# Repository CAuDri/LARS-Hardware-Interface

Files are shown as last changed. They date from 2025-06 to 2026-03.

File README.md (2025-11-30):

# LARS Hardware Interface

This repository contains the schematic, PCB design files and a basic firmware stack for the Hardware Interface of the [Lightweight Autonomous Racing System (LARS)](https://github.com/CAuDri/LARS). 

<p align="center">
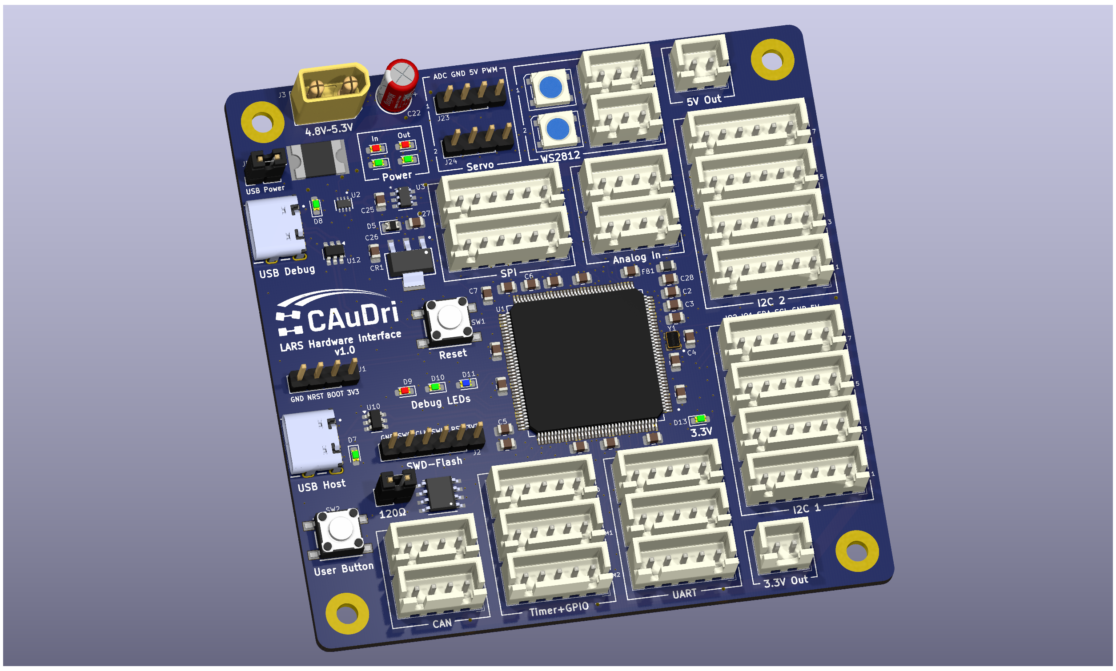
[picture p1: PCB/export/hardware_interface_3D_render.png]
  
</p>

The board is based on a STM32F4 microcontroller and is designed to interface with various sensors and actuators on the vehicle. The communication with the host PC is done via USB, using [micro-ROS](https://micro.ros.org/) and the underlying [micro-XRCE DDS](https://micro-xrce-dds.docs.eprosima.com/en/latest/).

## License

This project is licensed under the [GNU General Public License v3.0](https://www.gnu.org/licenses/gpl-3.0.en.html). You can freely use, modify, and distribute this code as long as you comply with the terms of the license.

The hardware design files are released under the [CERN Open Hardware Licence v2](https://ohwr.org/cernohl/).

# Hardware

##  Features

### General
- STM32F429 microcontroller (Cortex-M4, 180MHz, 2MB Flash, 256KB RAM)
- Board dimensions: 86 x 86 mm
- SWD interface for programming and debugging
- Boot-/Reset header for flashing via USB
- User- and Reset buttons
- RGB Debug LEDs

### Power
- 5V power supply via XT30 connector or USB (XT30 will be prioritized)
- Power input range: **4.8V - 5.3V**
- "Reverse polarity protection"
- On-board 3.3V voltage regulator
- Switchable 5V output for external devices
- Additional 3.3V and 5V output

### Interfaces
- 2x USB-C (2.0 Fullspeed) for host PC and debugging/flashing
- CAN-Bus (with optional termination)
- 8x I2C
- 3x UART
- 2x SPI
- 2x Servo (with analog feedback)
- 2x WS2812 LED strip 
- Buffered and filtered analog inputs
- Additional Timer channels and GPIOs
- 3.3V and 5V output for external devices

### Protection
- 4A/8A polyfuse on the main power input
- "Rudimentary" reverse polarity protection
- Back-power protection for both power inputs (USB and XT30)
- TVS diodes against voltage spikes on all power rails
- Current limited 5V output (max 2.4 A)
- All data lines are 5V tolerant
- Additional short-circuit, overcurrent and -voltage protection up to ~20V on all interfaces

## PCB-Files

The board was designed in KiCad 9.0. The project file can be found in the `/PCB/KiCad` directory.

Link to the [Schematic](https://github.com/CAuDri/LARS-Hardware-Interface/blob/main/PCB/schematic.pdf).

All PCB design files, a bill of materials and Gerber Files for manufacturing at [JLCPCB](https://jlcpcb.com/) can be found in the `/PCB/manufacturing` directory. They have been exported using the [Fabrication Toolkit](https://github.com/bennymeg/Fabrication-Toolkit) KiCad plugin.

A 3D STEP model of the board can be found in the `/PCB/export` directory.

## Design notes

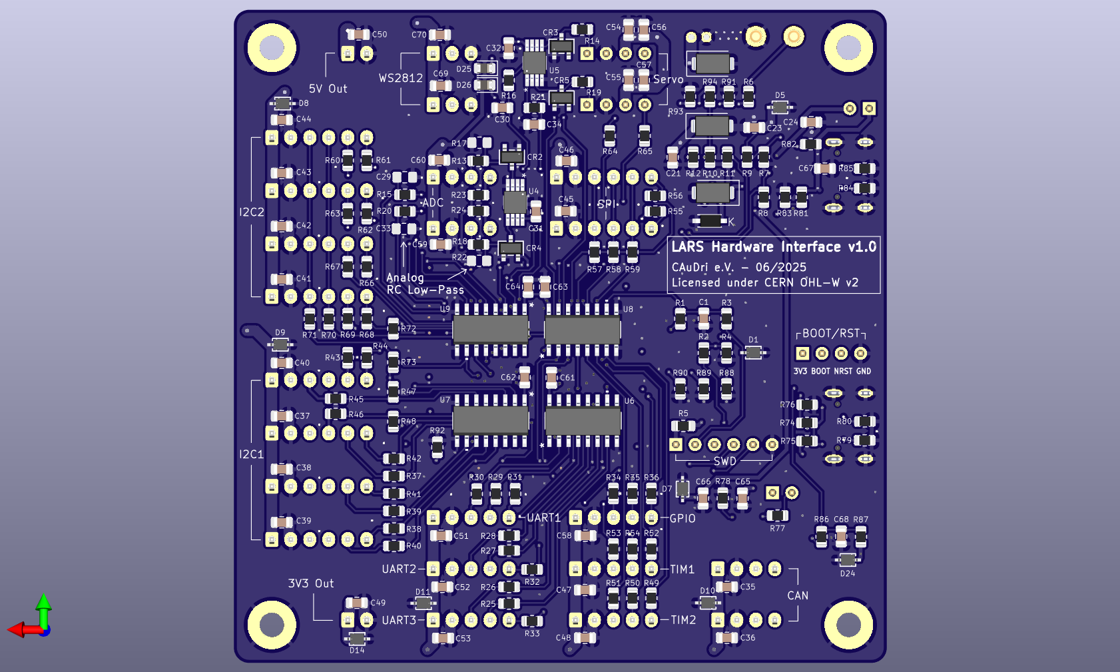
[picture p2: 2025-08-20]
PCB/export/hardware_interface_3D_back.png

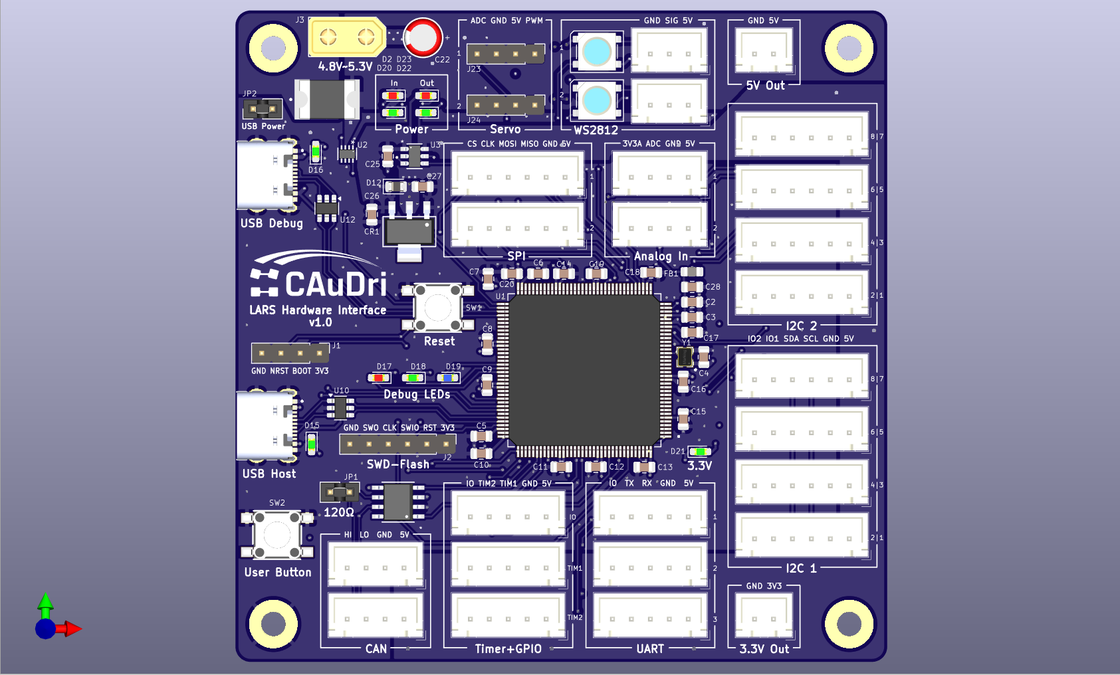
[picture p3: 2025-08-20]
PCB/export/hardware_interface_3D_front.png

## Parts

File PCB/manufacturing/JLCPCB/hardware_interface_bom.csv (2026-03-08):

Designator | Footprint | Quantity | Value | LCSC Part #
C1, C10, C11, C12, C13, C14, C15, C16, C17, C18, C19, C20, C3, C30, C31, C32, C34, C35, C36, C37, C38, C39, C4, C40, C41, C42, C43, C44, C45, C46, C47, C48, C49, C50, C51, C52, C53, C54, C57, C58, C59, C60, C61, C62, C63, C64, C65, C66, C67, C70, C71, C8, C9 | 0805 | 53 | 100n
C2, C24, C26, C5, C6, C68, C69 | 0805 | 7 | 2u2
C21, C23, C25, C27, C55, C56, C7 | 0805 | 7 | 10u
C22 | 860020372006 | 1 | 100u
C28 | 0805 | 1 | 10n
CR1 | LD1117AS33TR | 1 | LD1117AS33TR
CR2, CR3, CR4, CR5 | BAT54SFILM | 4 | BAT54SFILM
D1, D10, D11, D14, D24, D5, D7, D8, D9 | STS321050U182 | 9 | TVS
D12, D25, D26 | 0805 | 3 | 0.7V
D13 | BZT52C3V3 | 1 | 3V3
D15, D16, D18, D20, D21, D22 | 0603 | 6 | Green
D17, D2, D23 | 0603 | 3 | Red
D19 | 0603 | 1 | Blue
D27, D28 | LED_WS2812B_PLCC4_5.0x5.0mm_P3.2mm | 2 | WS2812B
D3, D4, D6 | Z1SMA5.6 | 3 | 5V6
F1 | 2920L400_15MR | 1 | 2920L400
FB1 | 0805 | 1 | FBMH2012HM221-T8
G1 | CAuDri Logo | 1 | CAuDri-Logo
G2 | OSHWA Logo | 1 | LOGO
J1 | PinHeader_1x04_P2.54mm_Vertical | 1 | Reset Header
J10, J11, J8, J9 | JST_XH_B6B-XH-A_1x06_P2.50mm_Vertical | 4 | I2C1
J12 | JST_XH_B5B-XH-A_1x05_P2.50mm_Vertical | 1 | TIM1
J13 | JST_XH_B5B-XH-A_1x05_P2.50mm_Vertical | 1 | TIM2
J14, J15, J16, J17 | JST_XH_B6B-XH-A_1x06_P2.50mm_Vertical | 4 | I2C2
J18 | JST_XH_B2B-XH-A_1x02_P2.50mm_Vertical | 1 | 3.3V Out
J19 | JST_XH_B2B-XH-A_1x02_P2.50mm_Vertical | 1 | 5V Out
J2 | PinHeader_1x06_P2.54mm_Vertical | 1 | SWD Flash
J20 | JST_XH_B5B-XH-A_1x05_P2.50mm_Vertical | 1 | UART1
J21 | JST_XH_B5B-XH-A_1x05_P2.50mm_Vertical | 1 | UART2
J22 | JST_XH_B5B-XH-A_1x05_P2.50mm_Vertical | 1 | RC
J23 | JST_XH_B5B-XH-A_1x05_P2.50mm_Vertical | 1 | GPIO
J24 | PinHeader_1x04_P2.54mm_Vertical | 1 | Servo 1
J25 | PinHeader_1x04_P2.54mm_Vertical | 1 | Servo 2
J26 | JST_XH_B4B-XH-A_1x04_P2.50mm_Vertical | 1 | Analog 1
J27 | JST_XH_B4B-XH-A_1x04_P2.50mm_Vertical | 1 | Analog 2
J28 | GCT_USB4105-GF-A | 1 | USB1
J29 | GCT_USB4105-GF-A | 1 | USB2
J3 | XT30UPB-M | 1 | XT30
J30 | JST_XH_B3B-XH-A_1x03_P2.50mm_Vertical | 1 | LED1
J31 | JST_XH_B3B-XH-A_1x03_P2.50mm_Vertical | 1 | LED2
J4, J5 | JST_XH_B4B-XH-A_1x04_P2.50mm_Vertical | 2 | CAN1
J6, J7 | JST_XH_B6B-XH-A_1x06_P2.50mm_Vertical | 2 | SPI1
JP1 | PinHeader_1x02_P2.54mm_Jumper | 1 | CAN1
JP2 | PinHeader_1x02_P2.54mm_Jumper | 1 | USB Power
R1, R4, R7, R86 | 0805 | 4 | 10k
R10, R11, R79, R8, R80, R84, R85 | 0805 | 7 | 5k1
R12, R23, R24, R44, R45, R68, R69, R77 | 0805 | 8 | 120
R13, R14, R16, R18, R19, R2, R21, R6, R74, R78, R81, R87, R88, R89, R9, R90, R91, R92, R93, R94 | 0805 | 20 | 1k
R15, R20, R25, R26, R27, R28, R29, R3, R30, R31, R32, R33, R34, R35, R36, R37, R38, R39, R40, R41, R42, R43, R48, R49, R50, R51, R52, R53, R54, R55, R56, R57, R58, R59, R60, R61, R62, R63, R64, R65, R66, R67, R72, R73, R75, R82 | 0805 | 46 | 220
R46, R47, R70, R71, R76, R83 | 0805 | 6 | 2k2
R5 | 0805 | 1 | 0R
SW1 | 430182043816 | 1 | Reset
SW2 | 430182043816 | 1 | User Button
U1 | STM32F429ZIT6TR | 1 | STM32F429ZIT6TR
U10 | SN74LVC2G86 | 1 | SN74LVC2G86DCUR
U11, U13 | SOT-23-6 | 2 | USBLC6-2SC6
U12 | TCAN1057AVDRQ1 | 1 | TCAN1057AVDRQ1
U2 | PTPS2117DRLR | 1 | TPS2117DRLR
U3 | MIC2039AYM6-TR | 1 | MIC2039AYM6-TR
U4, U5 | OPA2834IDGKR | 2 | OPA2834IDGKR
U6, U7, U8, U9 | SN74S1051DR | 4 | SN74S1051DR
Y1 | WE-SPXO_IQXO-791 | 1 | IQXO-791 8.00MHz

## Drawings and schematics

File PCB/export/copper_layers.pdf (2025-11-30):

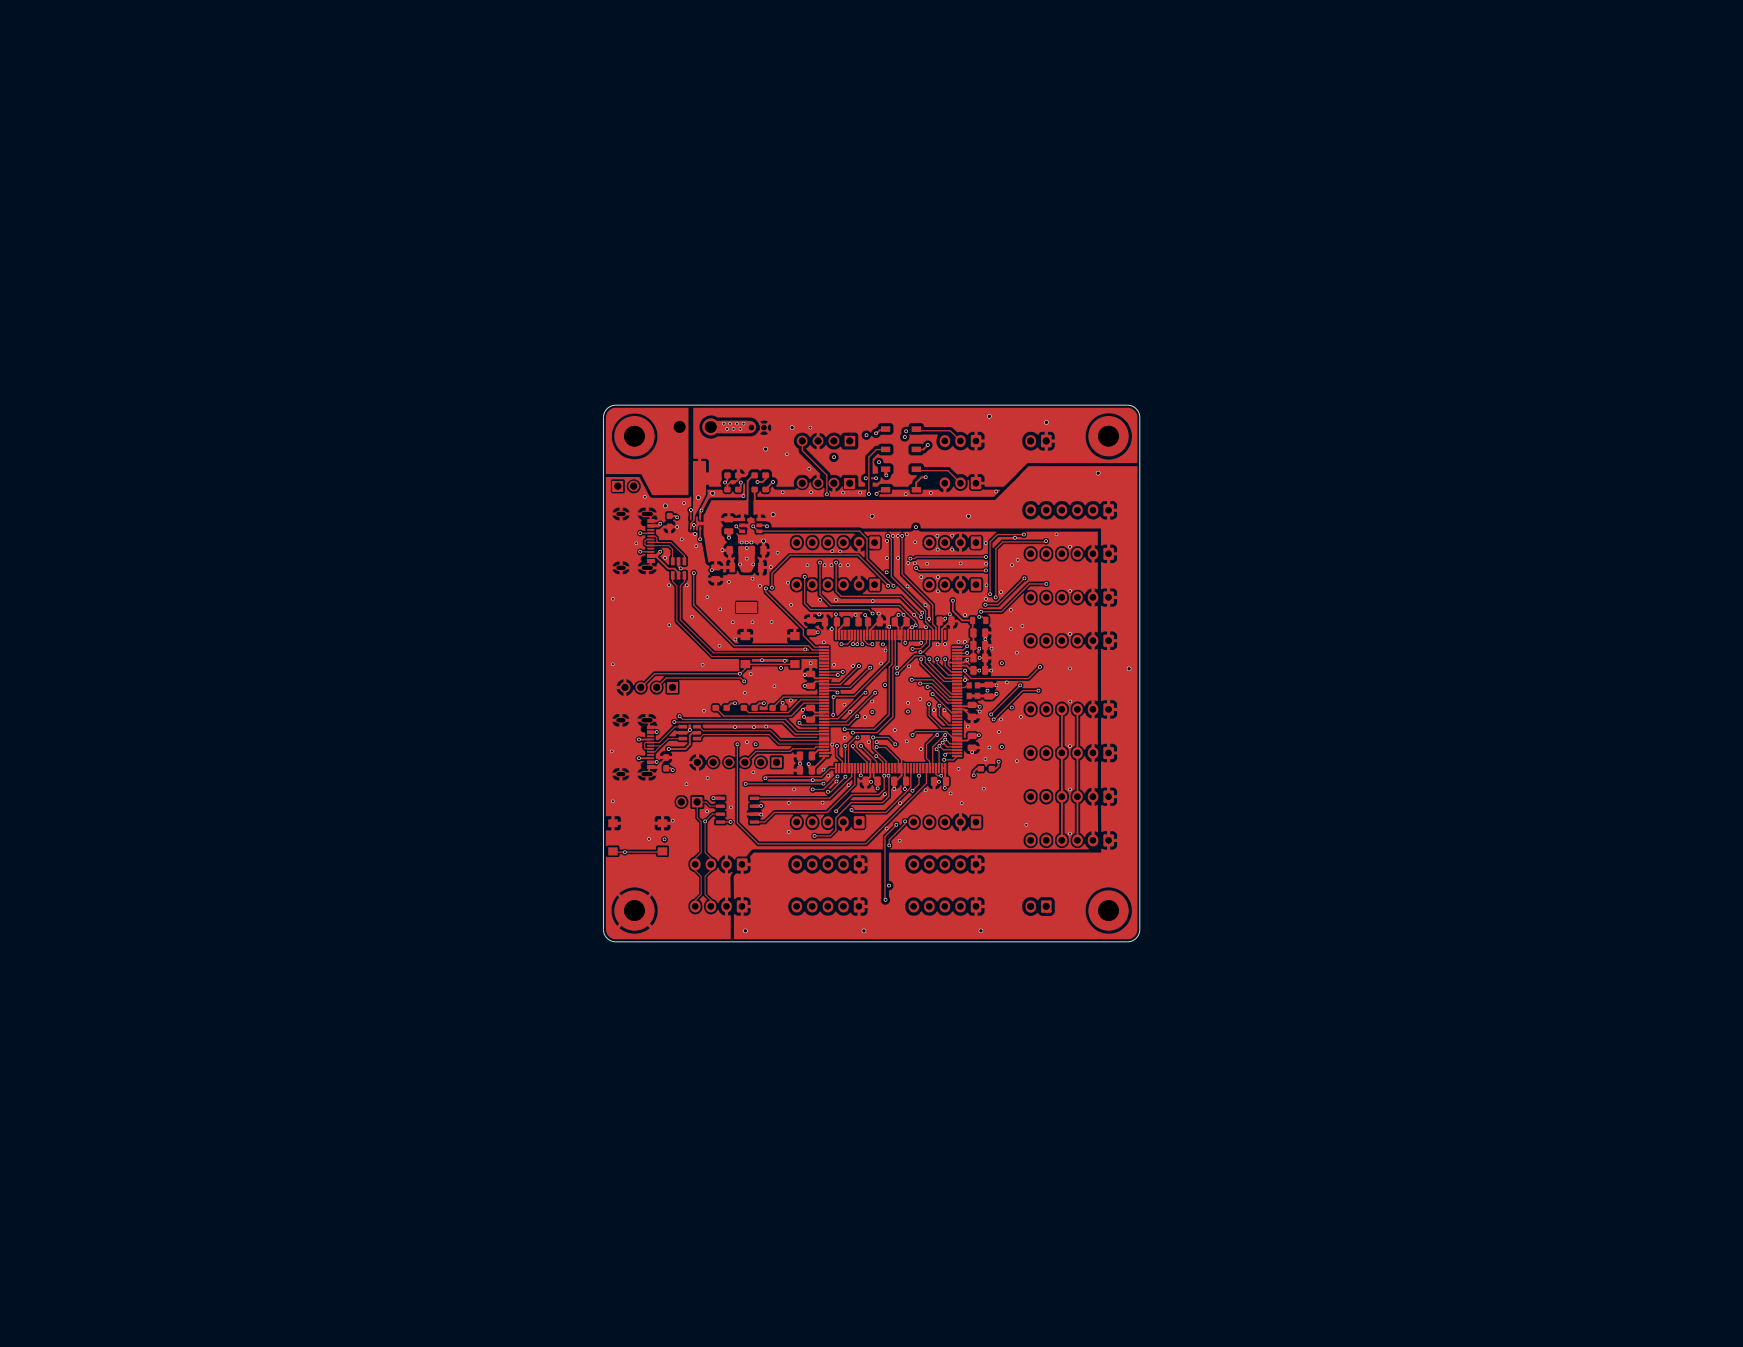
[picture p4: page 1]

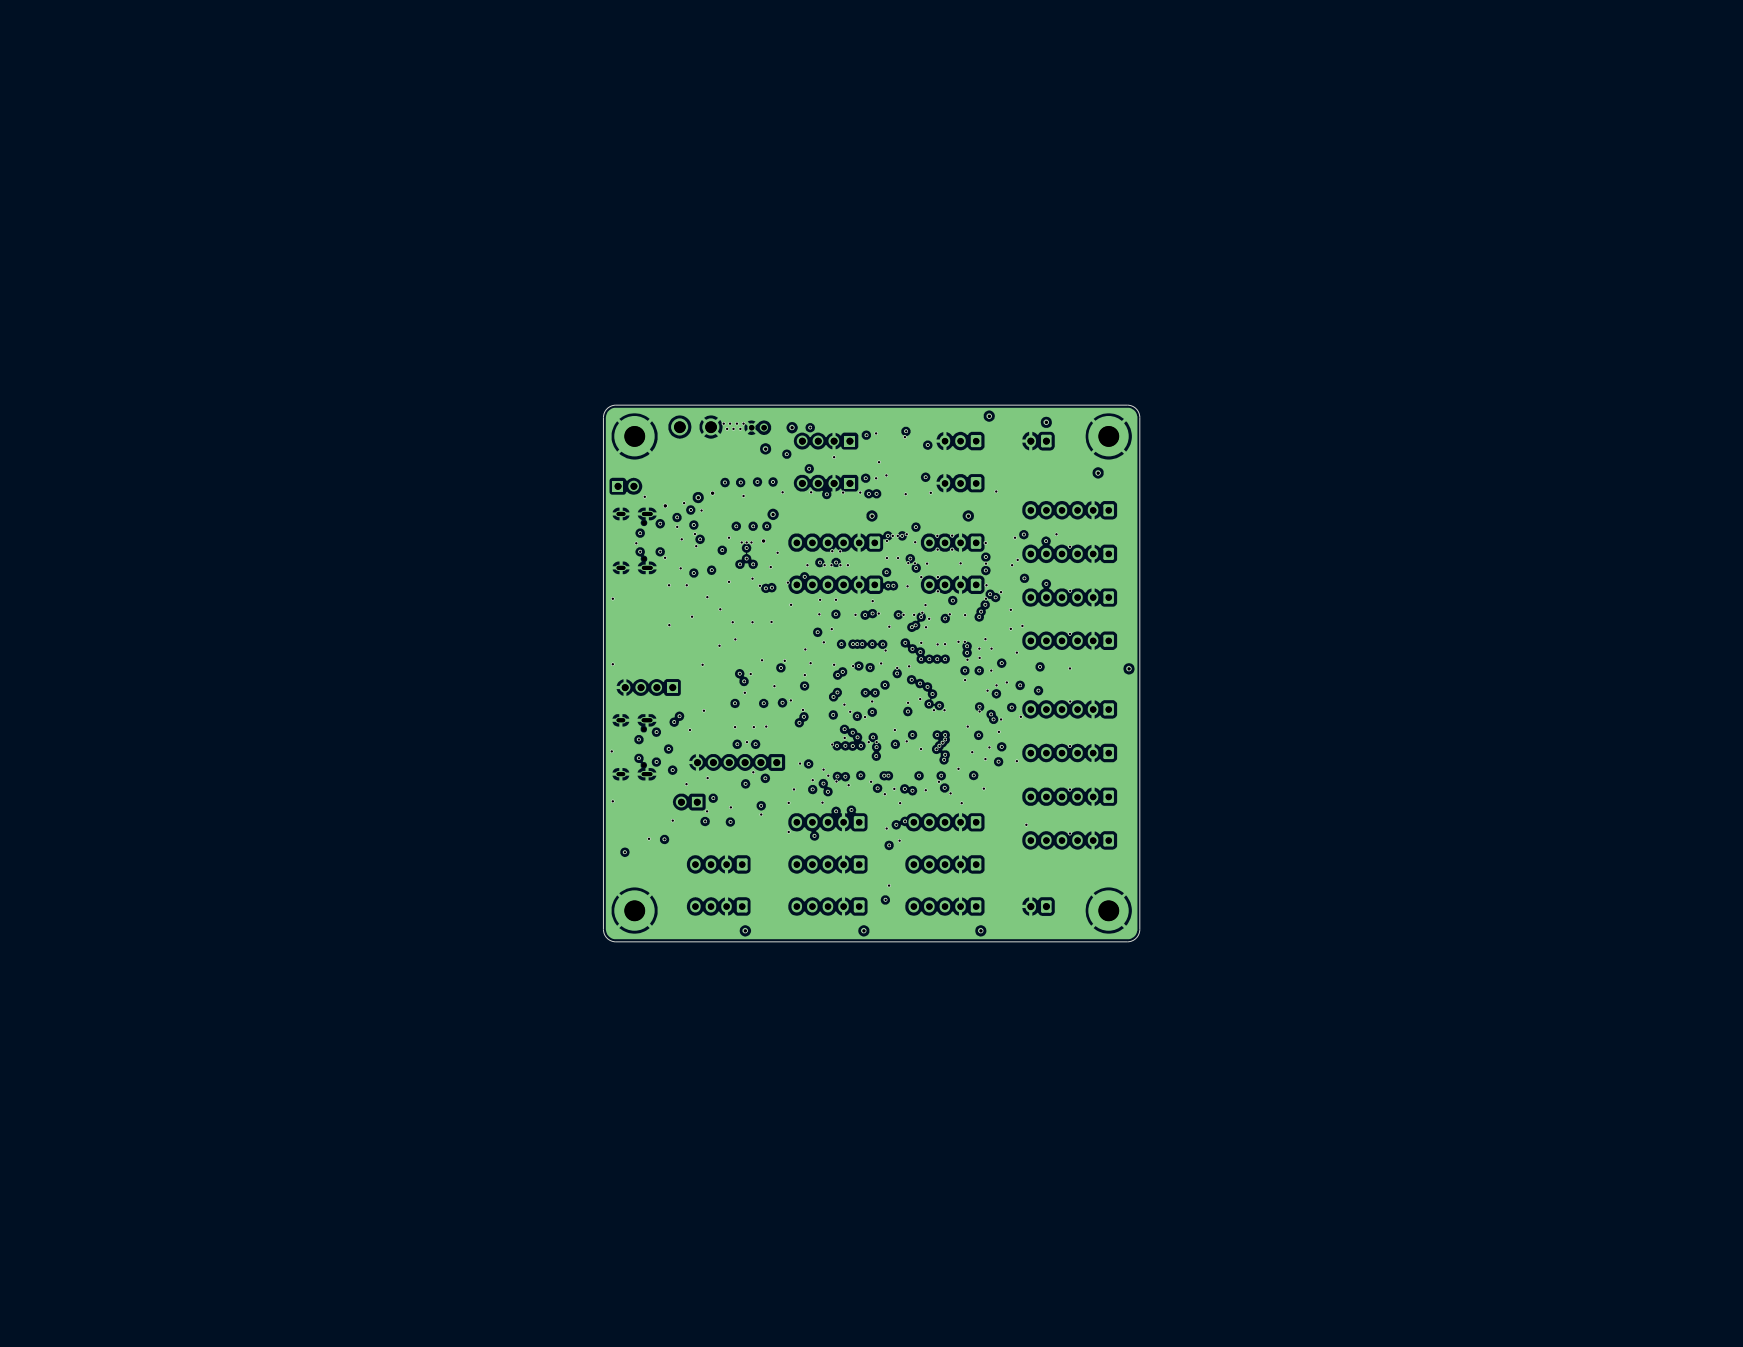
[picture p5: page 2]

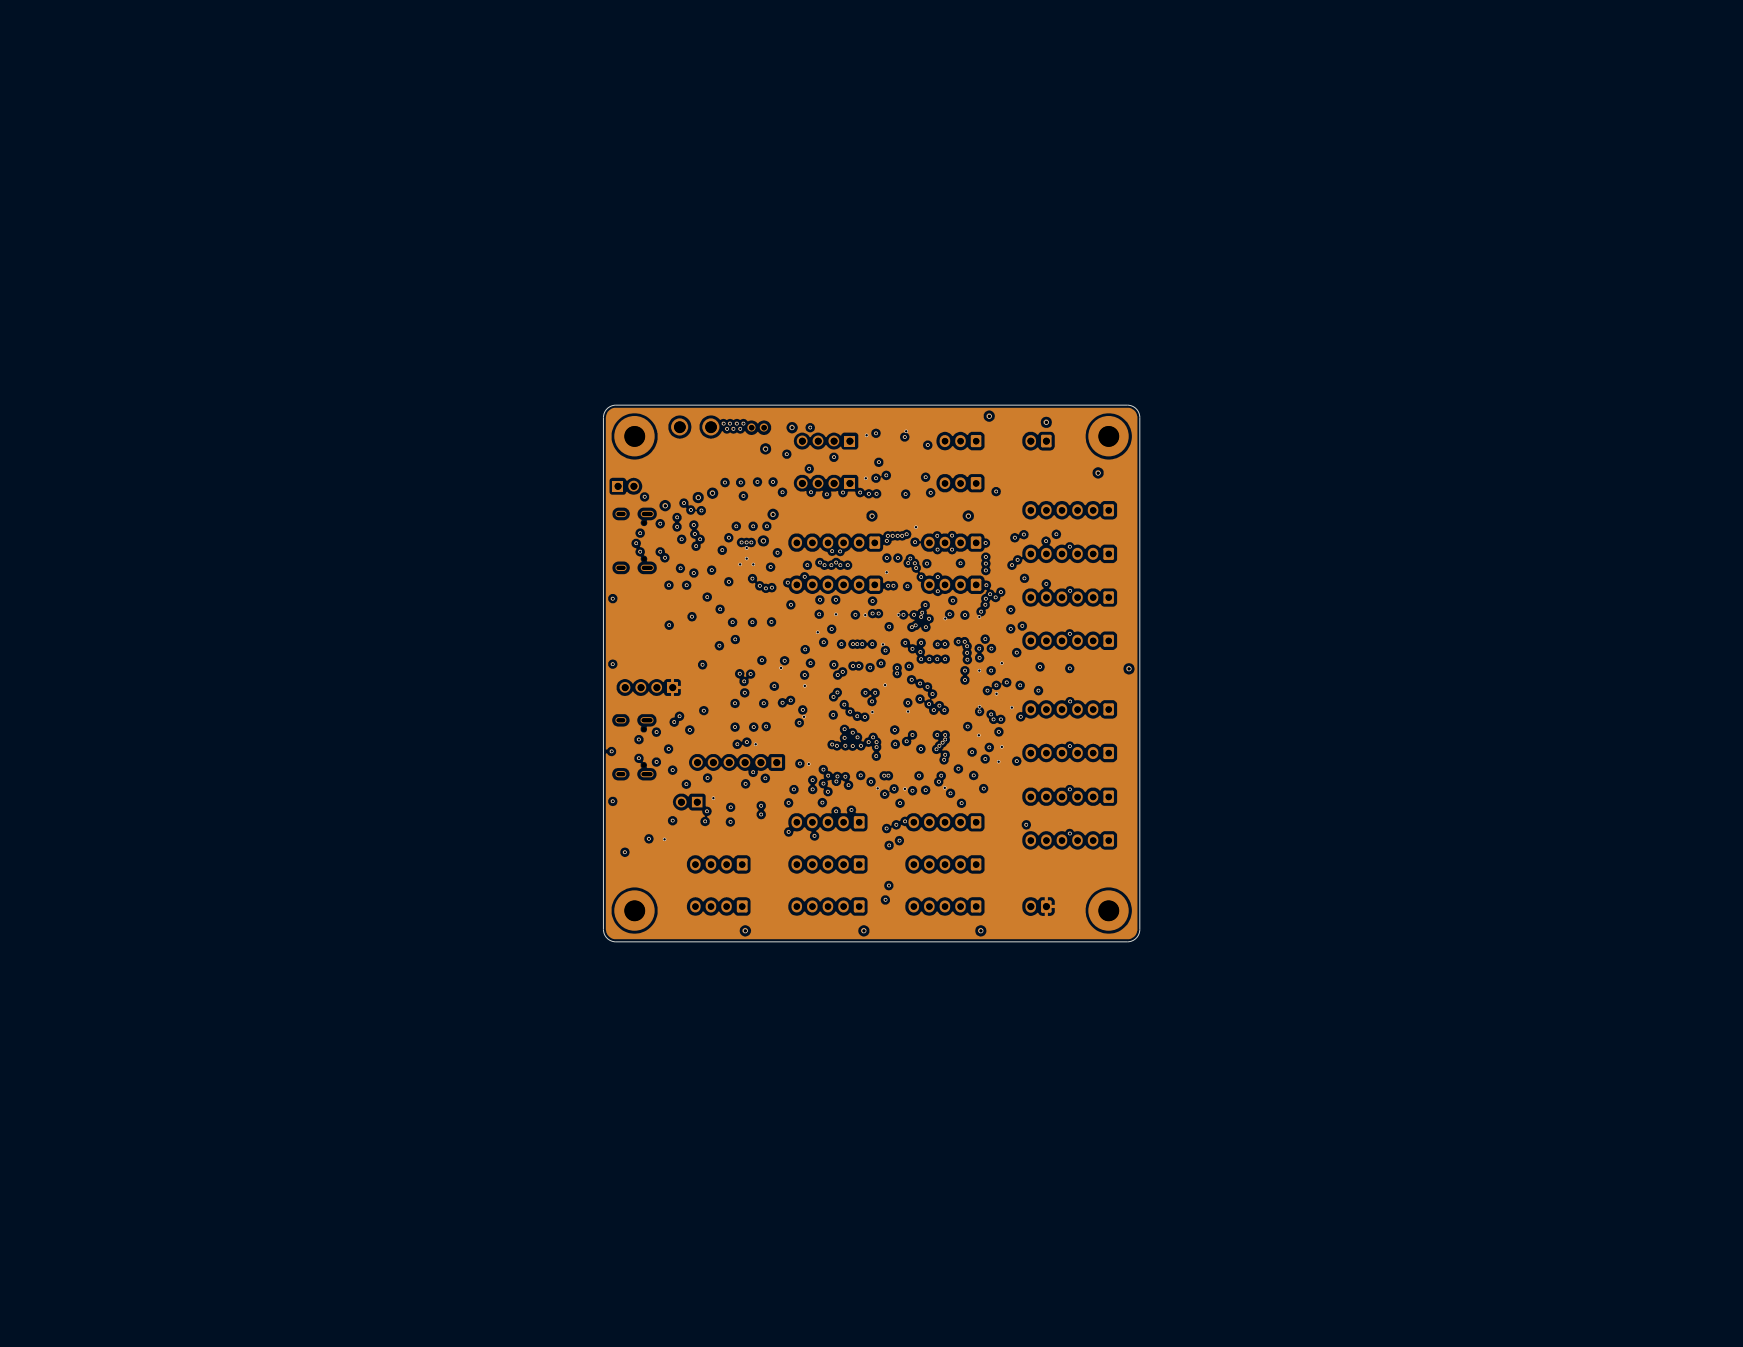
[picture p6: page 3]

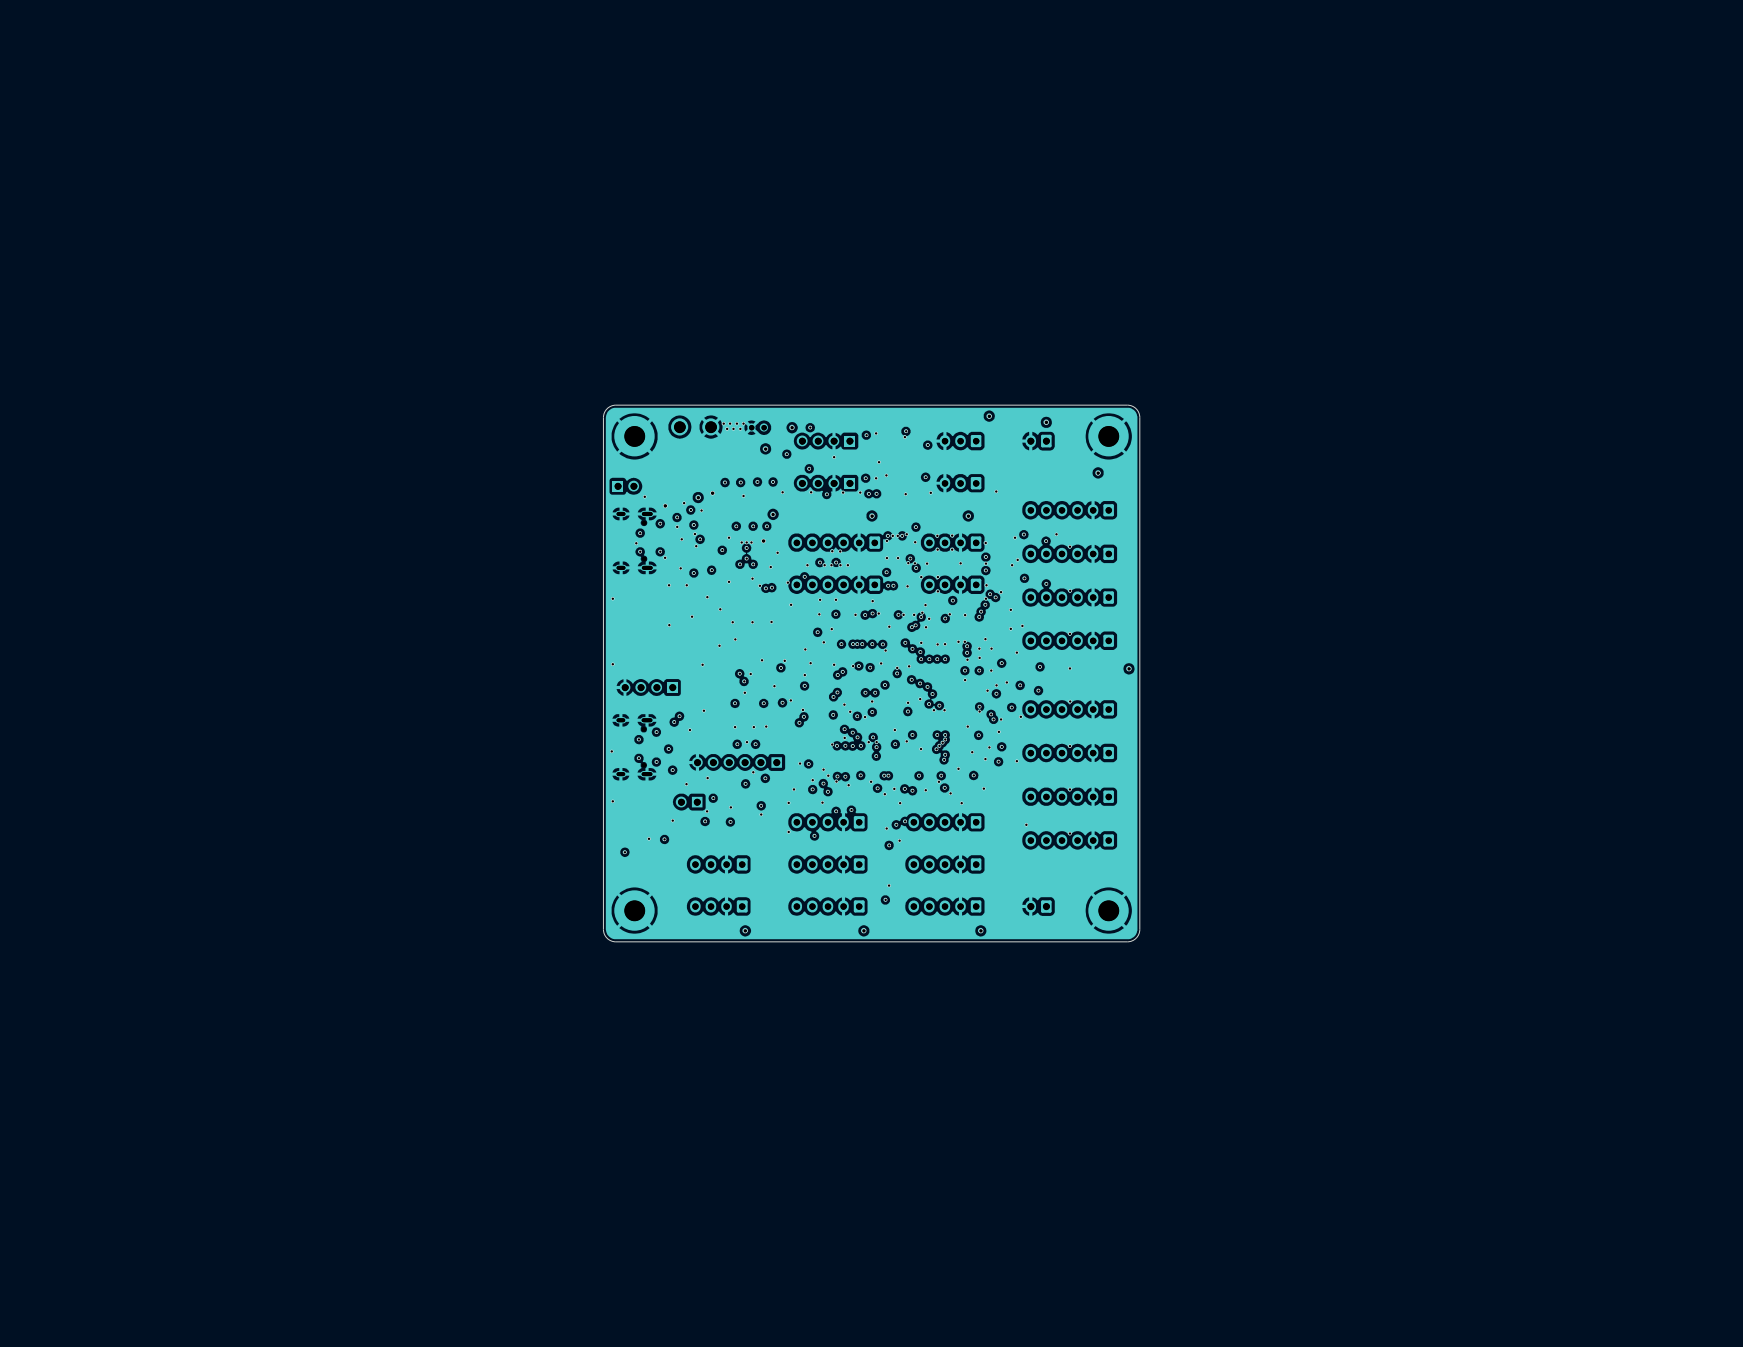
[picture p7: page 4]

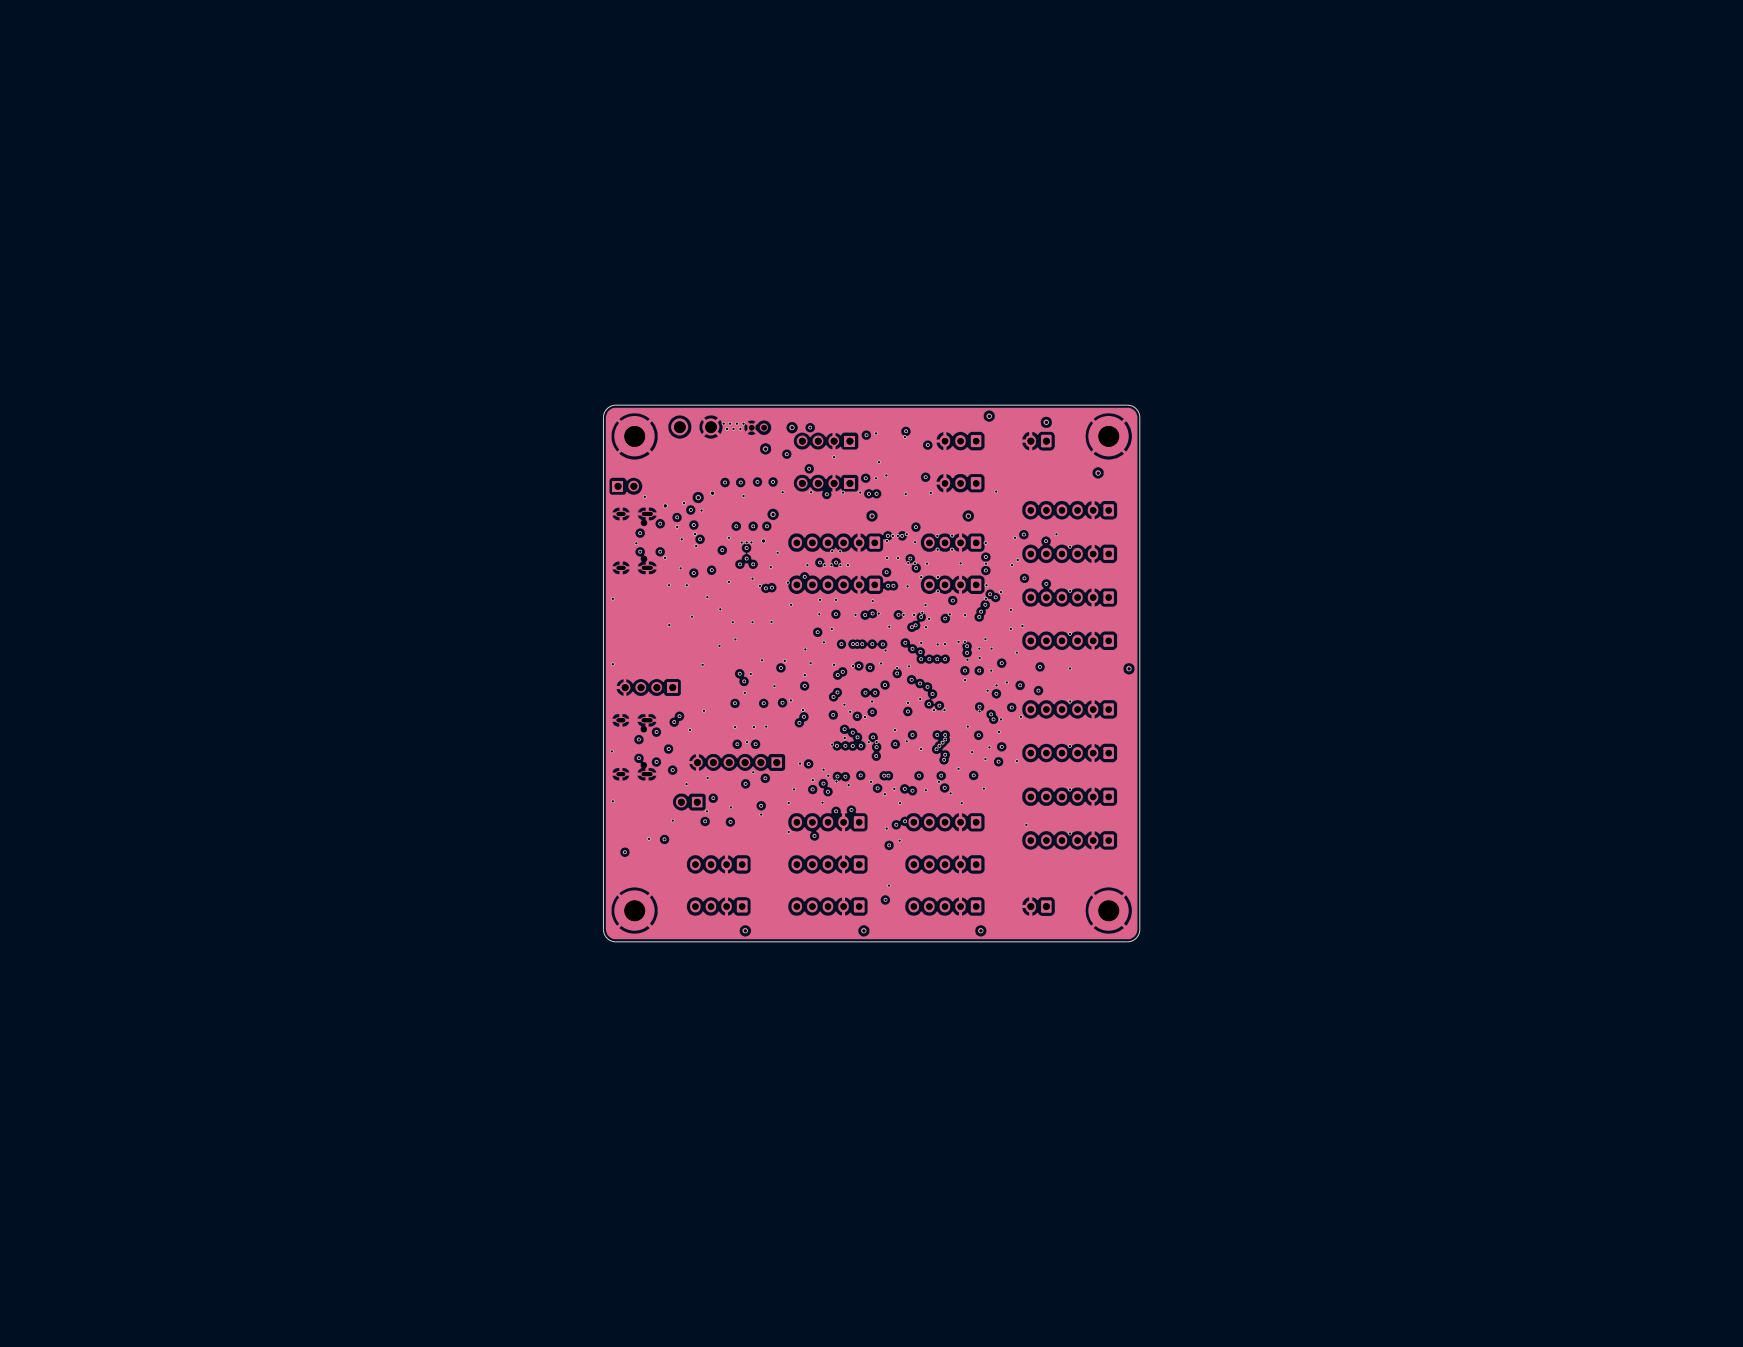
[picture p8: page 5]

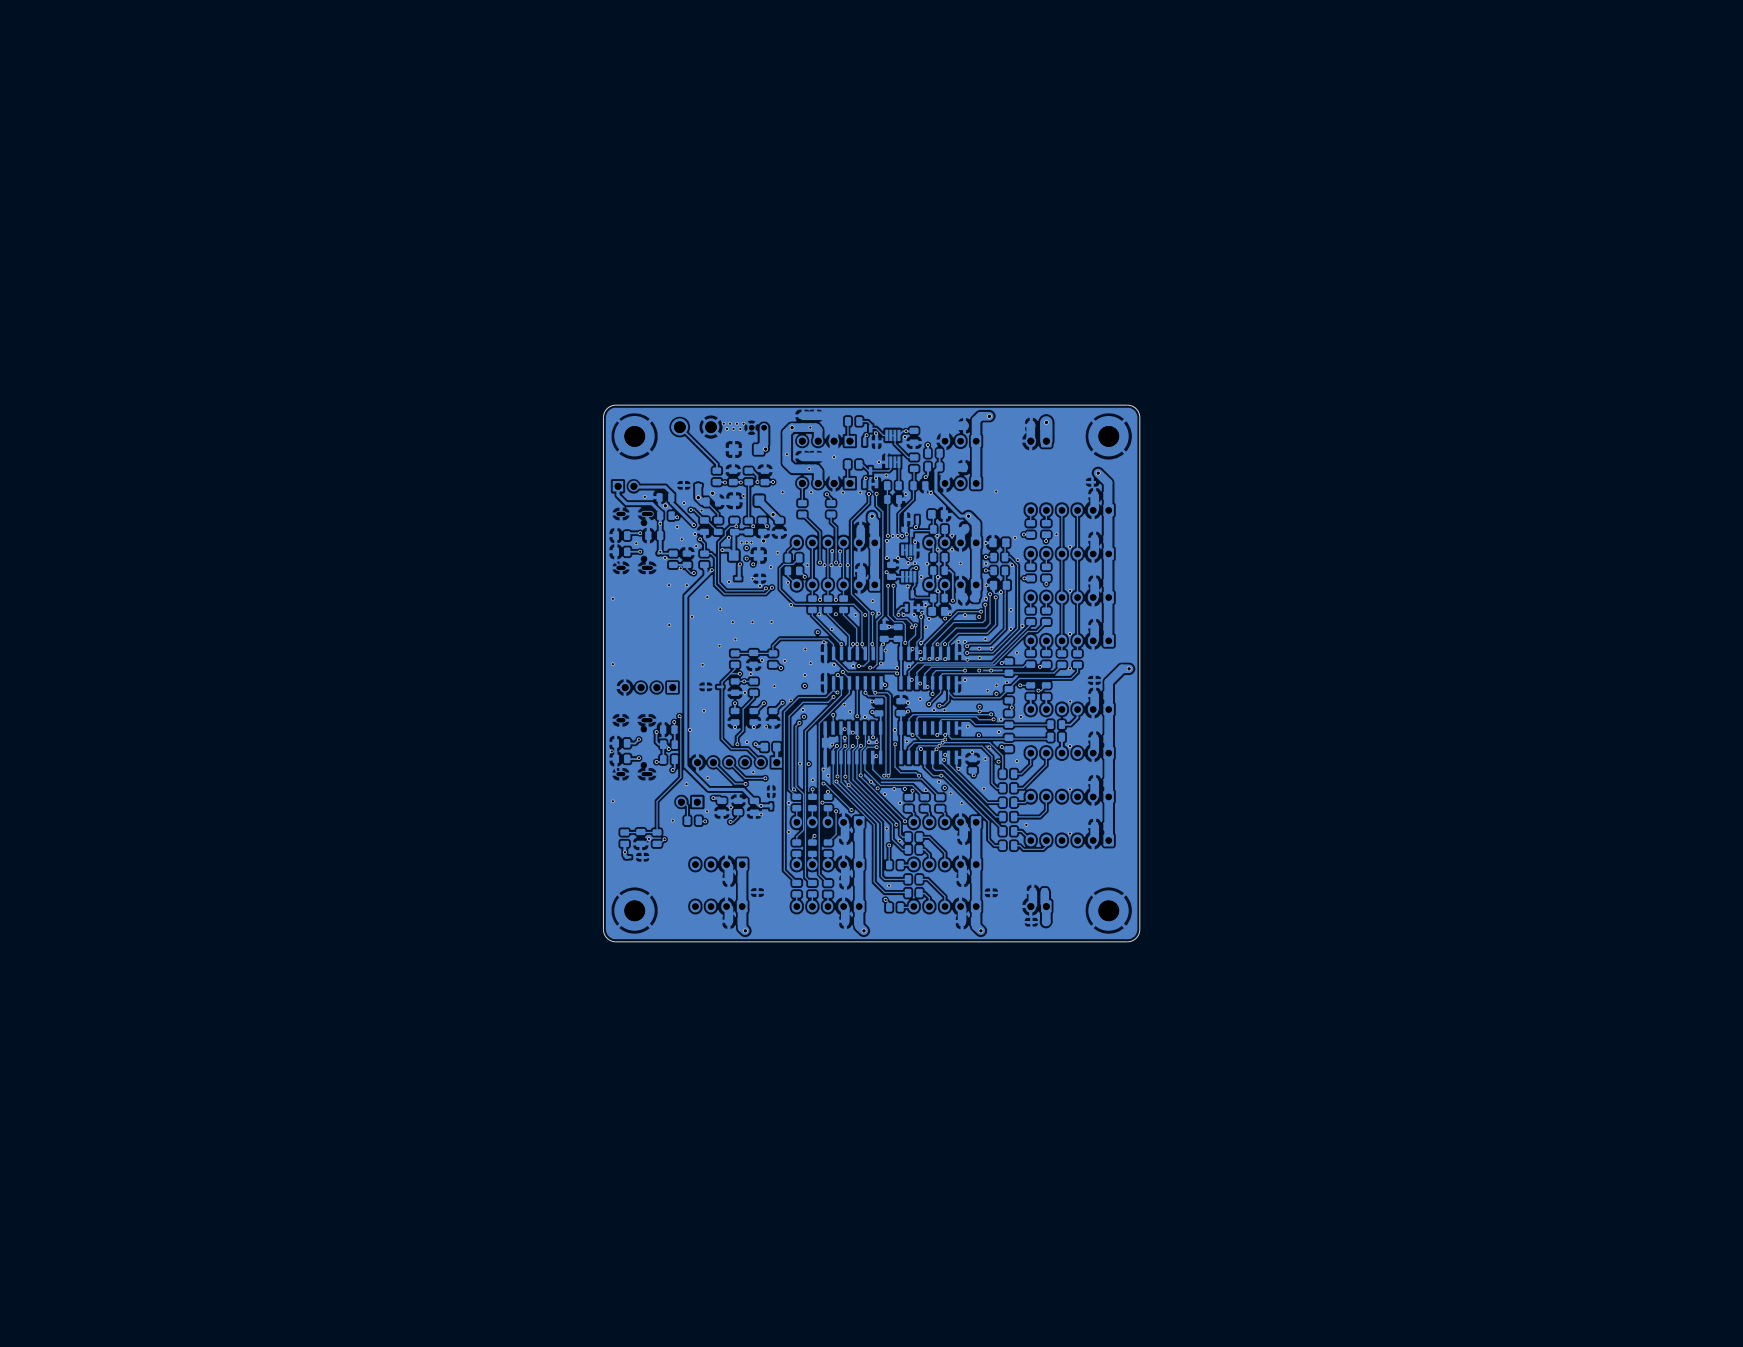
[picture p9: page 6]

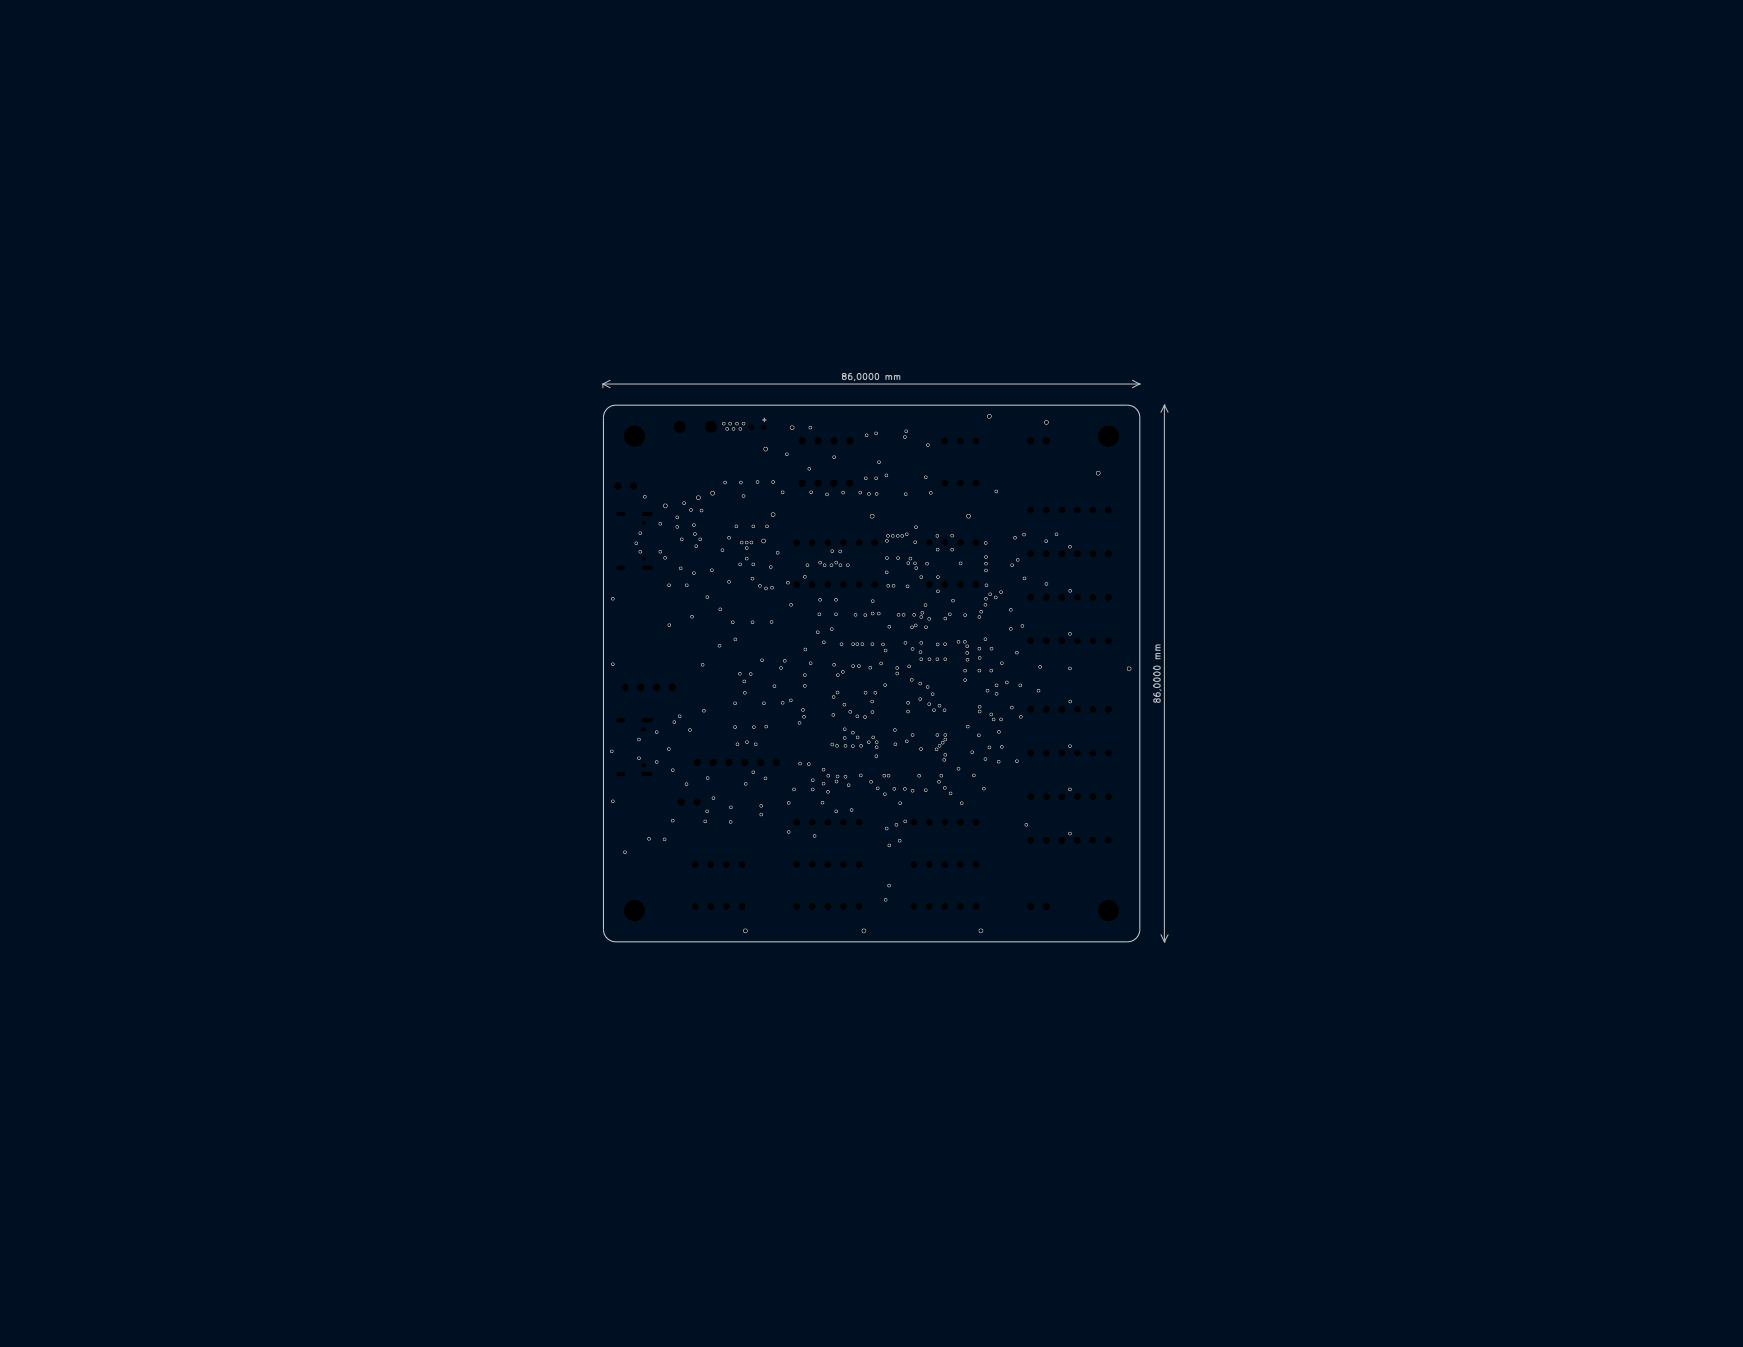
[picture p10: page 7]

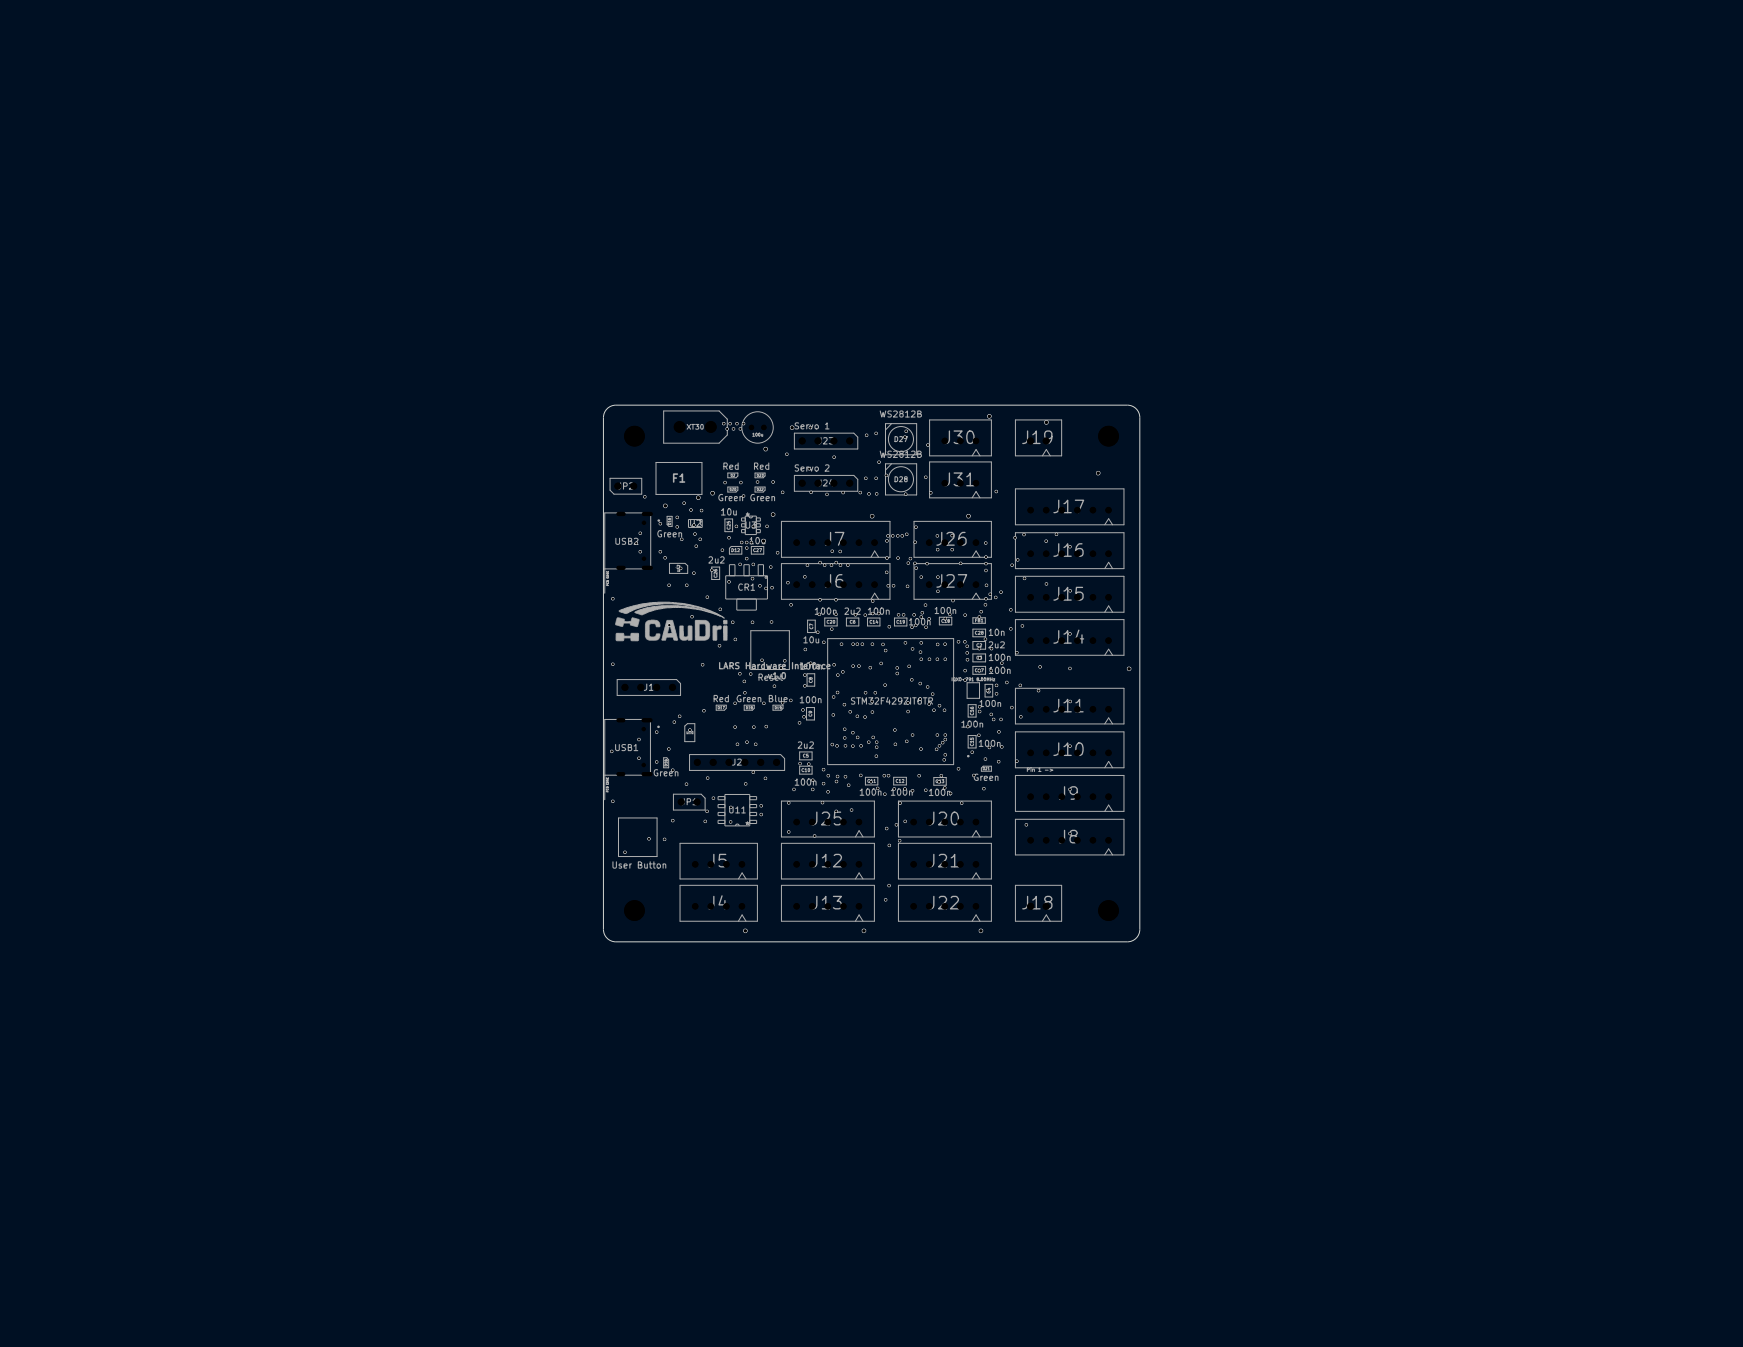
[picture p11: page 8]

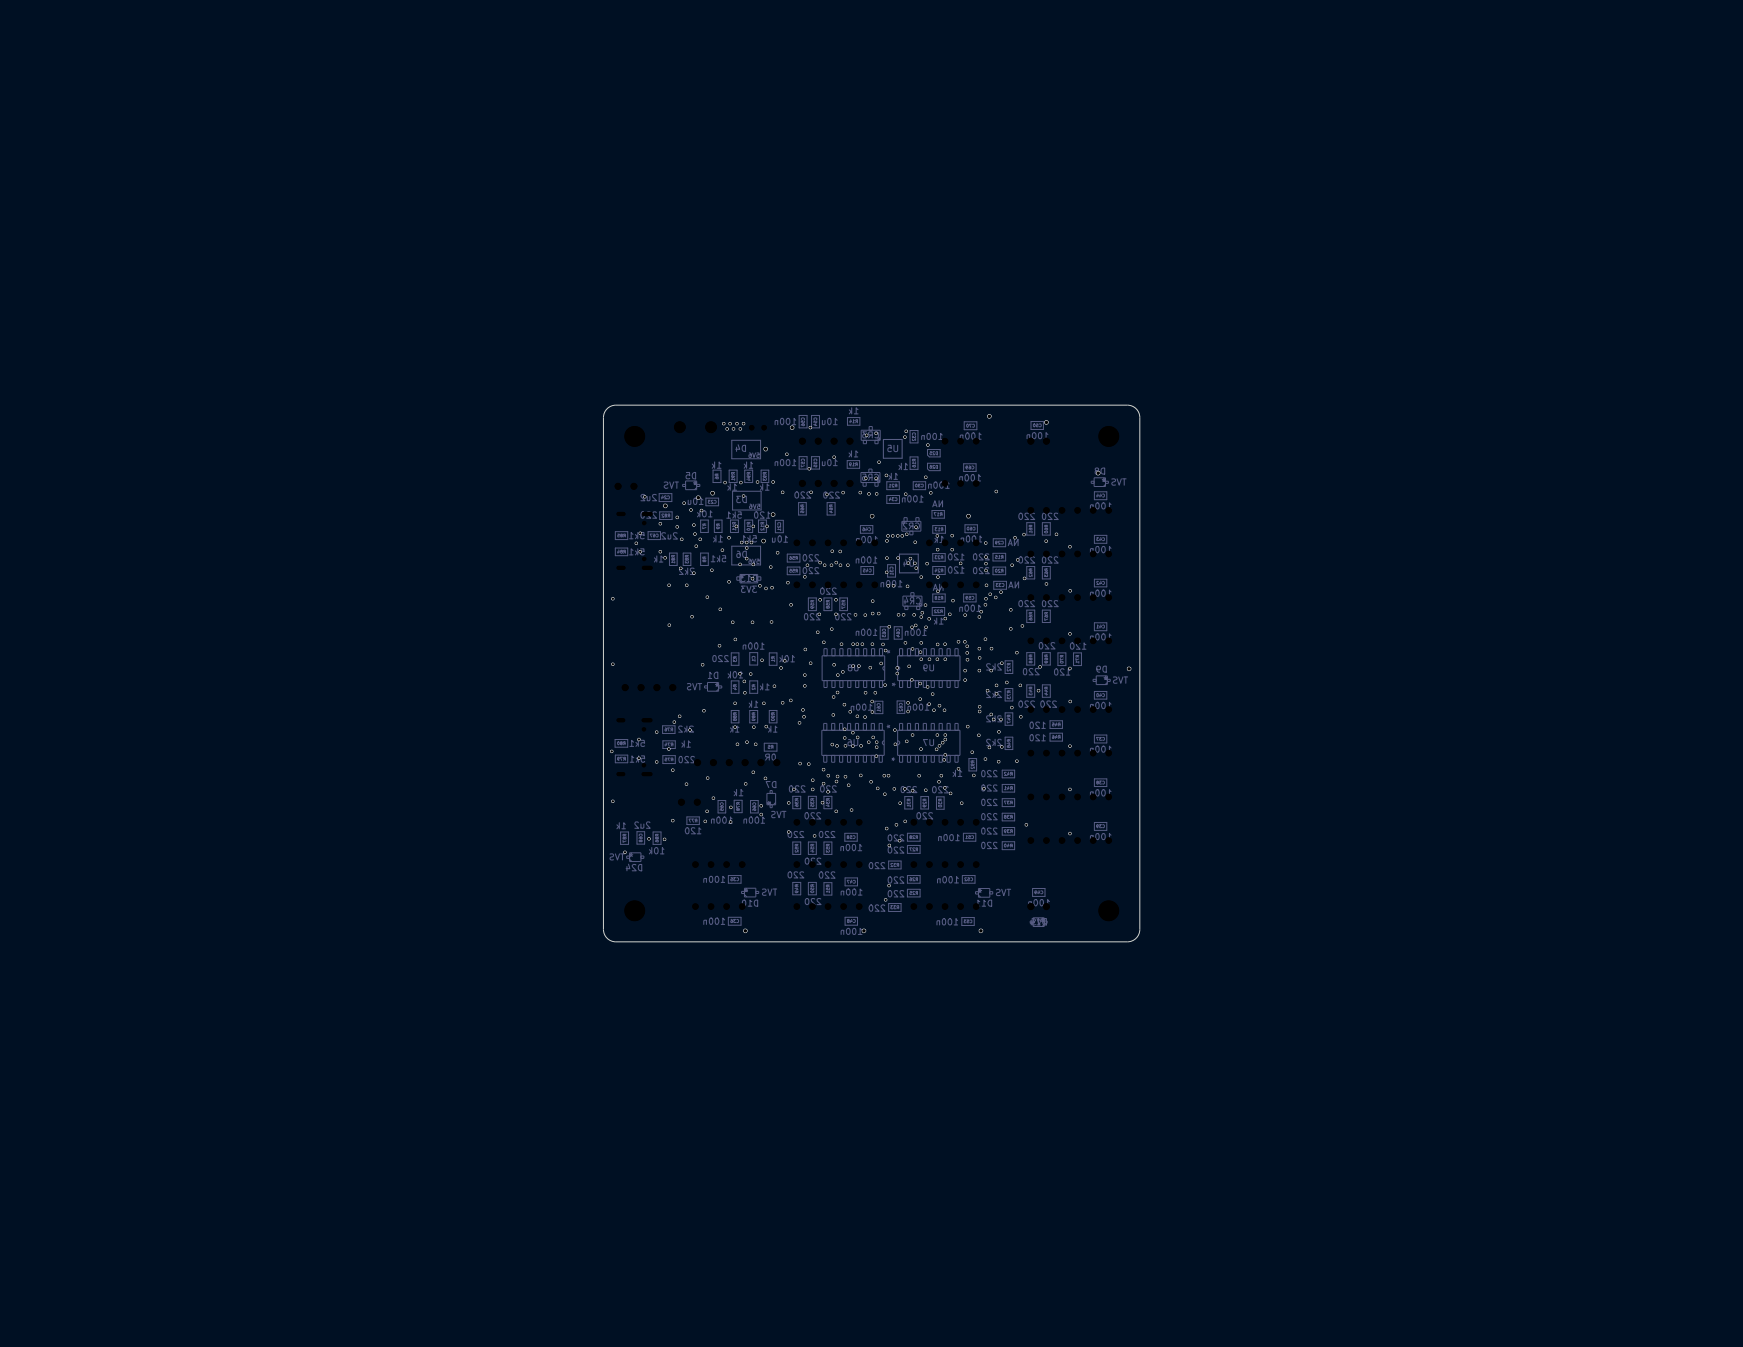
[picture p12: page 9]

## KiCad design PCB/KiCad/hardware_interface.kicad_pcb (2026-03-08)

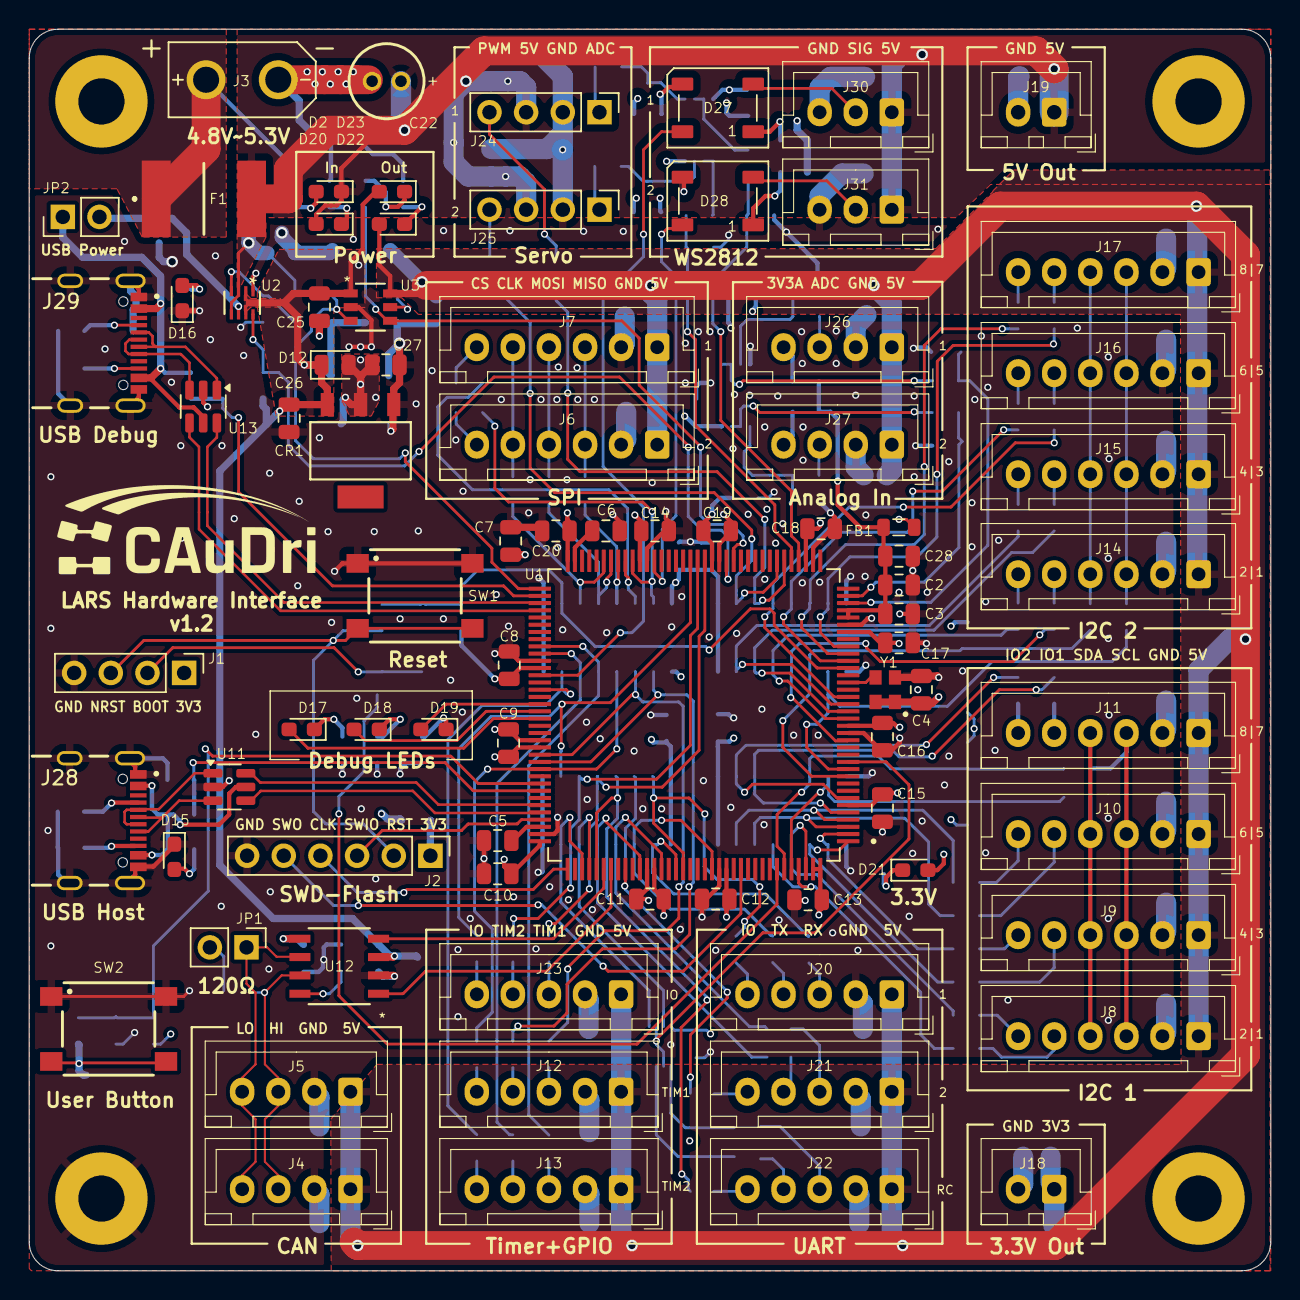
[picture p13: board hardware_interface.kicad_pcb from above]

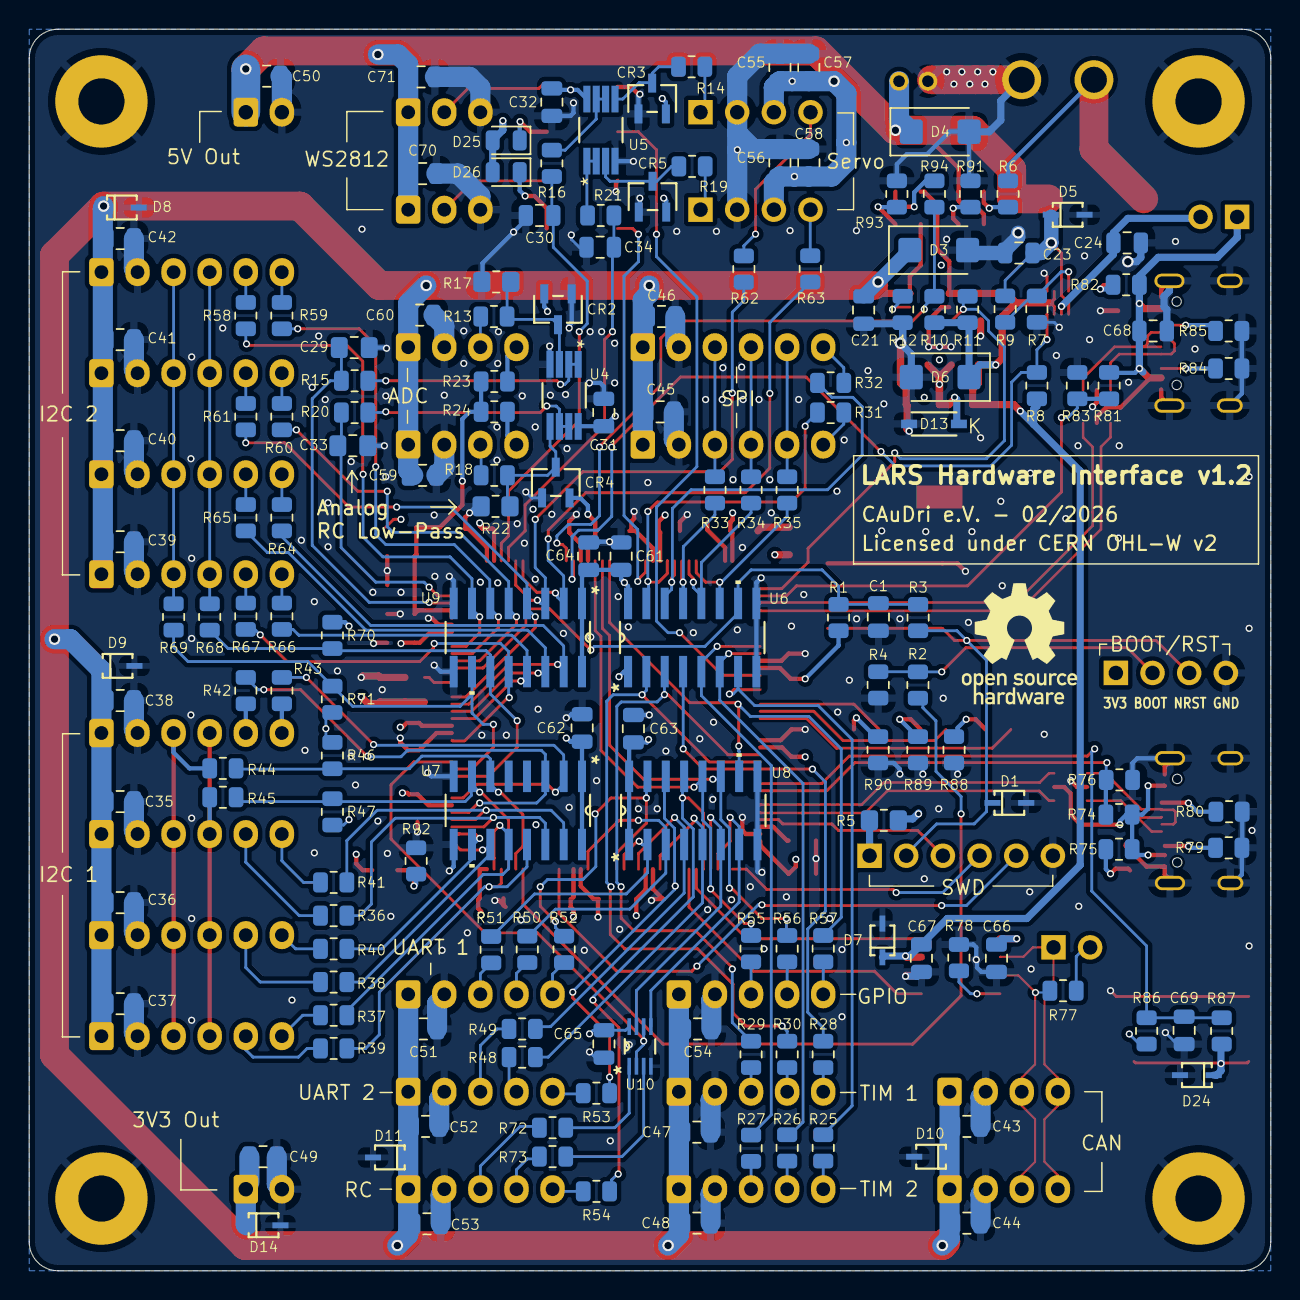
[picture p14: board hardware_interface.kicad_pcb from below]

Board: 6 copper layers, 86.0 x 86.0 mm, 255 parts (168 on the bottom side), 178 nets.

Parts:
C1, C3, C4, C8, C9, C10, C11, C12, C13, C14, C15, C16, C17, C18, C19, C20, C30, C31, C32, C34, C35, C36, C37, C38, C39, C40, C41, C42, C43, C44, C45, C46, C47, C48, C49, C50, C51, C52, C53, C54, C57, C58, C59, C60, C61, C62, C63, C64, C65, C66, C67, C70, C71: 100n; C_0805_2012Metric
C2, C5, C6, C24, C26, C68, C69: 2u2; C_0805_2012Metric
C7, C21, C23, C25, C27, C55, C56: 10u; C_0805_2012Metric
C22: 100u; 860020372006
C28: 10n; C_0805_2012Metric
C29, C33: NA; C_0805_2012Metric_Pad1.18x1.45mm_HandSolder
CR1: LD1117AS33TR
CR2, CR3, CR4, CR5: BAT54SFILM
D1, D5, D7, D8, D9, D10, D11, D14, D24: TVS; STS321050U182
D2, D17, D23: Red; LED_0603_1608Metric_Red
D3, D4, D6: 5V6; Z1SMA5.6
D12, D25, D26: 0.7V; D_0805_2012Metric
D13: 3V3; BZT52C3V3
D15, D16, D18, D20, D21, D22: Green; LED_0603_1608Metric_Green
D19: Blue; LED_0603_1608Metric_Blue
D27, D28: WS2812B; LED_WS2812B_PLCC4_5.0x5.0mm_P3.2mm
F1: 2920L400; 2920L400_15MR
FB1: FBMH2012HM221-T8; L_0805_2012Metric
G1: CAuDri-Logo; CAuDri Logo
G2: LOGO; OSHWA Logo
H1, H2, H3, H4: MountingHole; MountingHole_3.2mm_M3_Pad
J1: Reset Header; PinHeader_1x04_P2.54mm_Vertical
J2: SWD Flash; PinHeader_1x06_P2.54mm_Vertical
J3: XT30; XT30UPB-M
J4, J5: CAN1; JST_XH_B4B-XH-A_1x04_P2.50mm_Vertical
J6, J7: SPI1; JST_XH_B6B-XH-A_1x06_P2.50mm_Vertical
J8, J9, J10, J11: I2C1; JST_XH_B6B-XH-A_1x06_P2.50mm_Vertical
J12: TIM1; JST_XH_B5B-XH-A_1x05_P2.50mm_Vertical
J13: TIM2; JST_XH_B5B-XH-A_1x05_P2.50mm_Vertical
J14, J15, J16, J17: I2C2; JST_XH_B6B-XH-A_1x06_P2.50mm_Vertical
J18: 3.3V Out; JST_XH_B2B-XH-A_1x02_P2.50mm_Vertical
J19: 5V Out; JST_XH_B2B-XH-A_1x02_P2.50mm_Vertical
J20: UART1; JST_XH_B5B-XH-A_1x05_P2.50mm_Vertical
J21: UART2; JST_XH_B5B-XH-A_1x05_P2.50mm_Vertical
J22: RC; JST_XH_B5B-XH-A_1x05_P2.50mm_Vertical
J23: GPIO; JST_XH_B5B-XH-A_1x05_P2.50mm_Vertical
J24: Servo 1; PinHeader_1x04_P2.54mm_Vertical
J25: Servo 2; PinHeader_1x04_P2.54mm_Vertical
J26: Analog 1; JST_XH_B4B-XH-A_1x04_P2.50mm_Vertical
J27: Analog 2; JST_XH_B4B-XH-A_1x04_P2.50mm_Vertical
J28: USB1; GCT_USB4105-GF-A
J29: USB2; GCT_USB4105-GF-A
J30: LED1; JST_XH_B3B-XH-A_1x03_P2.50mm_Vertical
J31: LED2; JST_XH_B3B-XH-A_1x03_P2.50mm_Vertical
JP1: CAN1; PinHeader_1x02_P2.54mm_Jumper
JP2: USB Power; PinHeader_1x02_P2.54mm_Jumper
R1, R4, R7, R86: 10k; R_0805_2012Metric
R2, R6, R9, R13, R14, R16, R18, R19, R21, R74, R78, R81, R87, R88, R89, R90, R91, R92, R93, R94: 1k; R_0805_2012Metric
R3, R15, R20, R25, R26, R27, R28, R29, R30, R31, R32, R33, R34, R35, R36, R37, R38, R39, R40, R41, R42, R43, R48, R49, R50, R51, R52, R53, R54, R55, R56, R57, R58, R59, R60, R61, R62, R63, R64, R65, R66, R67, R72, R73, R75, R82: 220; R_0805_2012Metric
R5: 0R; R_0805_2012Metric_Pad1.20x1.40mm_HandSolder
R8, R10, R11, R79, R80, R84, R85: 5k1; R_0805_2012Metric
R12, R23, R24, R44, R45, R68, R69, R77: 120; R_0805_2012Metric
R17, R22: NA; R_0805_2012Metric_Pad1.20x1.40mm_HandSolder
R46, R47, R70, R71, R76, R83: 2k2; R_0805_2012Metric
SW1: Reset; 430182043816
SW2: User Button; 430182043816
U1: STM32F429ZIT6TR
U2: TPS2117DRLR; PTPS2117DRLR
U3: MIC2039AYM6-TR
U4, U5: OPA2834IDGKR
U6, U7, U8, U9: SN74S1051DR
U10: SN74LVC2G86DCUR; SN74LVC2G86
U11, U13: USBLC6-2SC6; SOT-23-6
U12: TCAN1057AVDRQ1
Y1: IQXO-791 8.00MHz; WE-SPXO_IQXO-791

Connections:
5V_USB: C24.1, JP2.2 (B), U2.6 (VIN2)
+3V3: C4.1, C7.1, C8.1, C9.1, C10.1, C11.1, C12.1, C13.1, C14.1, C15.1, C16.1, C17.1, C18.1, C19.1, C20.1, C27.1, C31.1, C32.1, C49.1, C61.1, C62.1, C63.1, C64.1, C65.1, C66.1, CR1.2 (VOUT), CR2.2, CR3.2, CR4.2, CR5.2, D12.2 (A), D13.1 (K), D14.1 (K), D21.2 (A), FB1.1, J1.1, J18.1, R1.2, R5.2, R46.2, R47.2, R70.2, R71.2, R86.1, U1.6 (VBAT), U1.17 (VDD), U1.30 (VDD), U1.39 (VDD), U1.52 (VDD), U1.62 (VDD), U1.72 (VDD), U1.84 (VDD), U1.95 (VDD), U1.108 (VDD), U1.121 (VDD), U1.131 (VDD), U1.143 (PDR_ON), U1.144 (VDD), U4.8 (VS+), U5.8 (VS+), U6.1 (VCC), U6.16 (VCC), U7.1 (VCC), U7.16 (VCC), U8.1 (VCC), U8.16 (VCC), U9.1 (VCC), U9.16 (VCC), U10.8 (VCC), U12.5 (VIO), Y1.1 (E/D), Y1.4 (+VS)
+3V3A: C2.1, C3.1, C28.1, FB1.2, R23.2, R24.2, U1.32 (VREF+), U1.33 (VDDA)
+5V: C25.1, C26.1, C67.1, CR1.3 (VIN), D6.1 (K), D7.1 (K), D12.1 (K), D23.2 (A), D25.2 (A), D26.2 (A), R8.1, R10.2, R11.2, U2.2 (VOUT), U2.7 (VOUT), U3.1 (VIN), U12.3 (VCC)
+5V_OUT: C21.1, C35.1, C36.1, C37.1, C38.1, C39.1, C40.1, C41.1, C42.1, C43.1, C44.1, C45.1, C46.1, C47.1, C48.1, C51.1, C52.1, C53.1, C54.1, C59.1, C60.1, D3.1 (K), D8.1 (K), D9.1 (K), D10.1 (K), D11.1 (K), D22.2 (A), J4.1, J5.1, J6.1, J7.1, J8.1, J9.1, J10.1, J11.1, J12.1, J13.1, J14.1, J15.1, J16.1, J17.1, J20.1, J21.1, J22.1, J23.1, J26.1, J27.1, U3.6 (VOUT)
+5V_PS: C22.1, C23.1, C50.1, C55.1, C56.1, C57.1, C58.1, C70.1, C71.1, D2.1 (K), D4.1 (K), D5.1 (K), D20.2 (A), F1.2, J19.1, J24.3, J25.3, J30.1, J31.1, R9.2, U2.3 (VIN1), U2.5 (MODE)
/Analog/ANALOG1_OP_IN: CR2.3, R13.2, R17.1, U4.3 (VIN1+)
/Analog/ANALOG1_OP_OUT: R15.1, U4.1 (VOUT1), U4.2 (VIN1-)
/Analog/ANALOG2_OP_IN: CR4.3, R18.2, R22.1, U4.5 (VIN2+)
/Analog/ANALOG2_OP_OUT: R20.1, U4.6 (VIN2-), U4.7 (VOUT2)
/Analog/SERVO1_OP_IN: CR3.3, R14.2, U5.5 (VIN2+)
/Analog/SERVO1_OP_OUT: R16.1, U5.6 (VIN2-), U5.7 (VOUT2)
/Analog/SERVO2_OP_IN: CR5.3, R19.2, U5.3 (VIN1+)
/Analog/SERVO2_OP_OUT: R21.1, U5.1 (VOUT1), U5.2 (VIN1-)
/LEDs/LED1_OUT: D27.2 (DOUT), J30.2
/LEDs/LED1_VDD: D25.1 (K), D27.1 (VDD)
/LEDs/LED2_OUT: D28.2 (DOUT), J31.2
/LEDs/LED2_VDD: D26.1 (K), D28.1 (VDD)
/LEDs/LED_3V3: D21.1 (K), R92.1
/LEDs/LED_5V_OUT: D22.1 (K), R93.1
/LEDs/LED_5V_PS: D20.1 (K), R91.1
/LEDs/LED_BLUE: D19.1 (K), R90.1
/LEDs/LED_EXT_OC: D23.1 (K), R94.1
/LEDs/LED_GREEN: D18.1 (K), R89.1
/LEDs/LED_RED: D17.1 (K), R88.1
/LEDs/USER_BTN: D24.1 (K), R87.2, SW2.2
/Microcontroller/BOOT0: J1.2, R2.1, R4.2
/Microcontroller/RESET: D1.1 (K), J1.3, J2.2, R3.1, SW1.2
/Microcontroller/STM_BOOT0: R2.2, U1.138 (BOOT0)
/Microcontroller/STM_OSC_IN: U1.23 (PH0), Y1.3 (OUT)
/Microcontroller/STM_VCAP1: C6.1, U1.71 (VCAP_1)
/Microcontroller/STM_VCAP2: C5.1, U1.106 (VCAP_2)
/Power Distribution/MUX_PR1: R7.1, R9.1, U2.4 (PR1)
/Power Distribution/PS_ILIMIT: R12.1, U3.5 (ILIMIT)
/Power Distribution/PWR_IN: F1.1, J3.2 (PWR), R6.2
/USB + CAN Bus/USB1_CC1: J28.A5 (CC1), R80.1
/USB + CAN Bus/USB1_CC2: J28.B5 (CC2), R79.1
/USB + CAN Bus/USB1_D_IN+: J28.A6 (D+), J28.B6 (D+), U11.3 (I/O2)
/USB + CAN Bus/USB1_D_IN-: J28.A7 (D-), J28.B7 (D-), U11.1 (I/O1)
/USB + CAN Bus/USB1_VBUS_IN: J28.A4_B9 (VBUS), J28.B4_A9 (VBUS), R74.2, R75.1, U11.5 (VBUS)
/USB + CAN Bus/USB2_CC1: J29.A5 (CC1), R85.1
/USB + CAN Bus/USB2_CC2: J29.B5 (CC2), R84.1
/USB + CAN Bus/USB2_D_IN+: J29.A6 (D+), J29.B6 (D+), U13.3 (I/O2)
/USB + CAN Bus/USB2_D_IN-: J29.A7 (D-), J29.B7 (D-), U13.1 (I/O1)
/USB + CAN Bus/USB2_VBUS_IN: C68.1, J29.A4_B9 (VBUS), J29.B4_A9 (VBUS), JP2.1 (A), R81.2, R82.1, U13.5 (VBUS)
ANALOG_IN1: J26.3, R13.1
ANALOG_IN1': C29.1, R15.2, U1.34 (PA0)
ANALOG_IN2: J27.3, R18.1
ANALOG_IN2': C33.1, R20.2, U1.35 (PA1)
CAN1_N: J4.4, J5.4, JP1.1 (A), U12.6 (CANL)
CAN1_P: J4.3, J5.3, R77.1, U12.7 (CANH)
CAN1_RX: U1.114 (PD0), U12.4 (RXD)
CAN1_TX: U1.115 (PD1), U12.1 (TXD)
DEBUG_LED_BLUE: D19.2 (A), U1.89 (PG4)
DEBUG_LED_GREEN: D18.2 (A), U1.90 (PG5)
DEBUG_LED_RED: D17.2 (A), U1.91 (PG6)
GND: C1.2, C2.2, C3.2, C4.2, C5.2, C6.2, C7.2, C8.2, C9.2, C10.2, C11.2, C12.2, C13.2, C14.2, C15.2, C16.2, C17.2, C18.2, C19.2, C20.2, C21.2, C22.2, C23.2, C24.2, C25.2, C26.2, C27.2, C28.2, C29.2, C30.2, C31.2, C32.2, C33.2, C34.2, C35.2, C36.2, C37.2, C38.2, C39.2, C40.2, C41.2, C42.2, C43.2, C44.2, C45.2, C46.2, C47.2, C48.2, C49.2, C50.2, C51.2, C52.2, C53.2, C54.2, C55.2, C56.2, C57.2, C58.2, C59.2, C60.2, C61.2, C62.2, C63.2, C64.2, C65.2, C66.2, C67.2, C68.2, C69.2, C70.2, C71.2, CR1.1 (GND), CR2.1, CR3.1, CR4.1, CR5.1, D1.2 (A), D3.2 (A), D4.2 (A), D5.2 (A), D6.2 (A), D7.2 (A), D8.2 (A), D9.2 (A), D10.2 (A), D11.2 (A), D13.2 (A), D14.2 (A), D15.1 (K), D16.1 (K), D24.2 (A), D27.3 (VSS), D28.3 (VSS), H1.1, H2.1, H3.1, H4.1, J1.4, J2.6, J3.1 (GND), J4.2, J5.2, J6.2, J7.2, J8.2, J9.2, J10.2, J11.2, J12.2, J13.2, J14.2, J15.2, J16.2, J17.2, J18.2, J19.2, J20.2, J21.2, J22.2, J23.2, J24.2, J25.2, J26.2, J27.2, J28.A1_B12 (GND), J28.B1_A12 (GND), J28.S1 (SHIELD), J29.A1_B12 (GND), J29.B1_A12 (GND), J29.S1 (SHIELD), J30.3, J31.3, R4.1, R7.2, R12.2, R17.2, R22.2, R76.2, R78.1, R79.2, R80.2, R83.2, R84.2, R85.2, R88.2, R89.2, R90.2, R91.2, R92.2, R93.2, SW1.1, SW2.1, U1.16 (VSS), U1.31 (VSSA), U1.38 (VSS), U1.51 (VSS), U1.61 (VSS), U1.83 (VSS), U1.94 (VSS), U1.107 (VSS), U1.120 (VSS), U1.130 (VSS), U2.1 (GND), U3.2 (GND), U4.4 (VS-), U5.4 (VS-), U6.8 (GND), U6.9 (GND), U7.8 (GND), U7.9 (GND), U8.8 (GND), U8.9 (GND), U9.8 (GND), U9.9 (GND), U10.4 (GND), U11.2 (GND), U12.2 (GND), U13.2 (GND), Y1.2 (GND)
GPIO1: J23.3, R55.2
GPIO1': R55.1, U1.53 (PF13), U8.12 (D09)
GPIO2: J23.4, R56.2
GPIO2': R56.1, U1.54 (PF14), U8.11 (D08)
GPIO3: J23.5, R57.2
GPIO3': R57.1, U1.55 (PF15), U8.10 (D07)
I2C1_IO1: J8.5, R39.2
I2C1_IO1': R39.1, U1.141 (PE0), U7.13 (D10)
I2C1_IO2: J8.6, R38.2
I2C1_IO2': R38.1, U1.142 (PE1), U7.12 (D09)
I2C1_IO3: J9.5, R37.2
I2C1_IO3': R37.1, U1.1 (PE2), U7.11 (D08)
I2C1_IO4: J9.6, R36.2
I2C1_IO4': R36.1, U1.2 (PE3), U7.10 (D07)
I2C1_IO5: J10.5, R40.2
I2C1_IO5': R40.1, U1.3 (PE4), U7.14 (D11)
I2C1_IO6: J10.6, R41.2
I2C1_IO6': R41.1, U1.4 (PE5), U7.15 (D12)
I2C1_IO7: J11.5, R43.2
I2C1_IO7': R43.1, U1.5 (PE6), U7.3 (D02)
I2C1_IO8: J11.6, R42.2
I2C1_IO8': R42.1, U1.7 (PC13), U7.2 (D01)
I2C1_SCL: J8.3, J9.3, J10.3, J11.3, R44.2
I2C1_SCL': R44.1, R46.1, U1.139 (PB8), U7.6 (D05)
I2C1_SDA: J8.4, J9.4, J10.4, J11.4, R45.2
I2C1_SDA': R45.1, R47.1, U1.140 (PB9), U7.7 (D06)
I2C2_IO1: J14.5, R67.2
I2C2_IO1': R67.1, U1.15 (PF5), U9.12 (D09)
I2C2_IO2: J14.6, R66.2
I2C2_IO2': R66.1, U1.18 (PF6), U9.13 (D10)
I2C2_IO3: J15.5, R65.2
I2C2_IO3': R65.1, U1.19 (PF7), U9.14 (D11)
I2C2_IO4: J15.6, R64.2
I2C2_IO4': R64.1, U1.20 (PF8), U9.15 (D12)
I2C2_IO5: J16.5, R61.2
I2C2_IO5': R61.1, U1.21 (PF9), U9.4 (D03)
I2C2_IO6: J16.6, R60.2
I2C2_IO6': R60.1, U1.26 (PC0), U9.5 (D04)
I2C2_IO7: J17.5, R58.2
I2C2_IO7': R59.1, U1.27 (PC1), U9.6 (D05)
I2C2_IO8: J17.6, R59.2
I2C2_IO8': R58.1, U1.28 (PC2), U9.7 (D06)
I2C2_SCL: J14.3, J15.3, J16.3, J17.3, R69.2
I2C2_SCL': R69.1, R71.1, U1.11 (PF1), U9.10 (D07)
I2C2_SDA: J14.4, J15.4, J16.4, J17.4, R68.2
I2C2_SDA': R68.1, R70.1, U1.10 (PF0), U9.11 (D08)
LED1_PWM: D27.4 (DIN), U1.85 (PD14)
LED2_PWM: D28.4 (DIN), U1.60 (PE9)
unnamed: D2.2 (A), R6.1
unnamed: D15.2 (A), R75.2
unnamed: D16.2 (A), R82.2
unnamed: J2.1, R5.1
unnamed: J26.4, R23.1
unnamed: J27.4, R24.1
unnamed: JP1.2 (B), R77.2
unnamed: R72.1, U10.1 (1A)
unnamed: R73.1, U10.3 (2Y)
unnamed: R78.2, U12.8 (S)
PWR_EXT_EN: R11.1, U1.73 (PB12), U3.3 (EN)
PWR_EXT_FAULT: R10.1, R94.2, U1.49 (PF11), U3.4 (*FAULT)
PWR_STATUS: R8.2, U1.50 (PF12), U2.8 (ST)
RC_INVERT: U1.12 (PF2), U10.2 (1B), U10.6 (2B)
RC_IO: J22.5, R54.2
RC_IO': R54.1, U1.113 (PC12), U8.13 (D10)
RC_RX: J22.3, R72.2
RC_RX': U1.112 (PC11), U8.6 (D05), U10.7 (1Y)
RC_TX: J22.4, R73.2
RC_TX': U1.111 (PC10), U8.7 (D06), U10.5 (2A)
SERVO1_ADC: J24.1, R14.1
SERVO1_ADC': C30.1, R16.2, U1.40 (PA4)
SERVO1_PWM: J24.4, R62.2
SERVO1_PWM': R62.1, U1.42 (PA6), U9.3 (D02)
SERVO2_ADC: J25.1, R19.1
SERVO2_ADC': C34.1, R21.2, U1.41 (PA5)
SERVO2_PWM: J25.4, R63.2
SERVO2_PWM': R63.1, U1.43 (PA7), U9.2 (D01)
SPI1_CS1: J6.6, R31.2
SPI1_CS1': R31.1, U1.63 (PE10), U6.15 (D12)
SPI1_CS2: J7.6, R32.2
SPI1_CS2': R32.1, U1.64 (PE11), U6.14 (D11)
SPI1_MISO: J6.4, J7.4, R34.2
SPI1_MISO': R34.1, U1.66 (PE13), U6.12 (D09)
SPI1_MOSI: J6.5, J7.5, R35.2
SPI1_MOSI': R35.1, U1.67 (PE14), U6.11 (D08)
SPI1_SCLK: J6.3, J7.3, R33.2
SPI1_SCLK': R33.1, U1.65 (PE12), U6.13 (D10)
STM_NRST: C1.1, R1.1, R3.2, U1.25 (~NRST), U6.10 (D07)
SWD_SWCLK: J2.4, U1.109 (PA14)
SWD_SWIO: J2.3, U1.105 (PA13)
SWD_SWO: J2.5, U1.133 (PB3)
TIM1_CH1: J12.3, R29.2
TIM1_CH1': R29.1, U1.96 (PC6), U6.3 (D02)
TIM1_CH2: J12.4, R30.2
TIM1_CH2': R30.1, U1.97 (PC7), U6.2 (D01)
TIM1_IO: J12.5, R28.2
TIM1_IO': R28.1, U1.98 (PC8), U6.4 (D03)
TIM2_CH1: J13.3, R27.2
TIM2_CH1': R27.1, U1.81 (PD12), U6.5 (D04)
TIM2_CH2: J13.4, R26.2
TIM2_CH2': R26.1, U1.82 (PD13), U6.6 (D05)
TIM2_IO: J13.5, R25.2
TIM2_IO': R25.1, U1.87 (PG2), U6.7 (D06)
UART1_IO: J20.5, R52.2
UART1_IO': R52.1, U1.125 (PG10), U8.15 (D12)
UART1_RX: J20.3, R51.2
UART1_RX': R51.1, U1.124 (PG9), U8.2 (D01)
UART1_TX: J20.4, R50.2
UART1_TX': R50.1, U1.129 (PG14), U8.3 (D02)
UART2_IO: J21.5, R53.2
UART2_IO': R53.1, U1.117 (PD3), U8.14 (D11)
UART2_RX: J21.3, R49.2
UART2_RX': R49.1, U1.122 (PD6), U8.4 (D03)
UART2_TX: J21.4, R48.2
UART2_TX': R48.1, U1.119 (PD5), U8.5 (D04)
USB1_D+: U1.104 (PA12), U11.4 (I/O2)
USB1_D-: U1.103 (PA11), U11.6 (I/O1)
USB1_VBUS: R74.1, R76.1, U1.101 (PA9)
USB2_D+: U1.76 (PB15), U13.4 (I/O2)
USB2_D-: U1.75 (PB14), U13.6 (I/O1)
USB2_VBUS: R81.1, R83.1, U1.74 (PB13)
USER_BUTTON: C69.1, R86.2, R87.1, U1.100 (PA8)

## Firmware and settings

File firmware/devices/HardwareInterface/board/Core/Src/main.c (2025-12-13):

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
/* Includes ------------------------------------------------------------------*/
#include "main.h"
#include "cmsis_os.h"
#include "usb_device.h"

/* USER CODE BEGIN Includes */

#include "logger.h"
#include "thread_safe_can.h"
#include "thread_safe_i2c.h"

/* USER CODE END Includes */

typedef StaticTask_t osStaticThreadDef_t;
ADC_HandleTypeDef hadc1;
ADC_HandleTypeDef hadc2;
DMA_HandleTypeDef hdma_adc1;
DMA_HandleTypeDef hdma_adc2;

CAN_HandleTypeDef hcan1;

I2C_HandleTypeDef hi2c1;
I2C_HandleTypeDef hi2c2;

SPI_HandleTypeDef hspi4;

TIM_HandleTypeDef htim3;
TIM_HandleTypeDef htim4;
TIM_HandleTypeDef htim5;
TIM_HandleTypeDef htim8;
DMA_HandleTypeDef hdma_tim4_ch3;

UART_HandleTypeDef huart2;
UART_HandleTypeDef huart3;
UART_HandleTypeDef huart6;
DMA_HandleTypeDef hdma_usart2_rx;
DMA_HandleTypeDef hdma_usart2_tx;
DMA_HandleTypeDef hdma_usart3_rx;
DMA_HandleTypeDef hdma_usart3_tx;
DMA_HandleTypeDef hdma_usart6_rx;
DMA_HandleTypeDef hdma_usart6_tx;

/* Definitions for mainTask */
osThreadId_t mainTaskHandle;
uint32_t mainTaskBuffer[ 4096 ];
osStaticThreadDef_t mainTaskControlBlock;
const osThreadAttr_t mainTask_attributes = {
  .name = "mainTask",
  .cb_mem = &mainTaskControlBlock,
  .cb_size = sizeof(mainTaskControlBlock),
  .stack_mem = &mainTaskBuffer[0],
  .stack_size = sizeof(mainTaskBuffer),
  .priority = (osPriority_t) osPriorityNormal,
};
void SystemClock_Config(void);
static void MX_GPIO_Init(void);
static void MX_DMA_Init(void);
static void MX_ADC1_Init(void);
static void MX_CAN1_Init(void);
static void MX_I2C1_Init(void);
static void MX_I2C2_Init(void);
static void MX_SPI4_Init(void);
static void MX_USART2_UART_Init(void);
static void MX_USART3_UART_Init(void);
static void MX_ADC2_Init(void);
static void MX_TIM3_Init(void);
static void MX_USART6_UART_Init(void);
static void MX_TIM4_Init(void);
static void MX_TIM8_Init(void);
static void MX_TIM5_Init(void);
void StartMainTask(void *argument);

/* USER CODE BEGIN PFP */

// CAuDri - Main entry point in main.cpp
extern void mainTask(); 

/* USER CODE END PFP */

/**
  * @brief  The application entry point.
  * @retval int
  */
int main(void)
{

  /* MCU Configuration--------------------------------------------------------*/

  /* Reset of all peripherals, Initializes the Flash interface and the Systick. */
  HAL_Init();

  /* Configure the system clock */
  SystemClock_Config();

  /* Initialize all configured peripherals */
  MX_GPIO_Init();
  MX_DMA_Init();
  MX_ADC1_Init();
  MX_CAN1_Init();
  MX_I2C1_Init();
  MX_I2C2_Init();
  MX_SPI4_Init();
  MX_USART2_UART_Init();
  MX_USART3_UART_Init();
  MX_ADC2_Init();
  MX_TIM3_Init();
  MX_USART6_UART_Init();
  MX_TIM4_Init();
  MX_TIM8_Init();
  MX_TIM5_Init();
  /* USER CODE BEGIN 2 */

  // CAuDri - Initialize the trace recorder for debugging with Tracealyzer
  #ifdef DEBUG_USE_TRACE_RECORDER
    xTraceInitialize();
  #endif

  /* USER CODE END 2 */

  /* Init scheduler */
  osKernelInitialize();

  /* USER CODE BEGIN RTOS_MUTEX */
  /* add mutexes, ... */
  /* USER CODE END RTOS_MUTEX */

  /* USER CODE BEGIN RTOS_SEMAPHORES */
  /* add semaphores, ... */
  /* USER CODE END RTOS_SEMAPHORES */

  /* USER CODE BEGIN RTOS_TIMERS */
  /* start timers, add new ones, ... */
  /* USER CODE END RTOS_TIMERS */

  /* USER CODE BEGIN RTOS_QUEUES */
  /* add queues, ... */
  /* USER CODE END RTOS_QUEUES */

  /* Create the thread(s) */
  /* creation of mainTask */
  mainTaskHandle = osThreadNew(StartMainTask, NULL, &mainTask_attributes);

  /* USER CODE BEGIN RTOS_THREADS */

  // CAuDri - Initialize the logging interface and start the logger thread
  if (!logger_init()) {
      LogInline("Main: Failed to initialize logger");
  } else {
      LogClear();
  }

  /* add threads, ... */
  /* USER CODE END RTOS_THREADS */

  /* USER CODE BEGIN RTOS_EVENTS */
  /* add events, ... */
  /* USER CODE END RTOS_EVENTS */

  /* Start scheduler */
  osKernelStart();

  /* We should never get here as control is now taken by the scheduler */

  /* Infinite loop */
  /* USER CODE BEGIN WHILE */
  while (1)
  {
    /* USER CODE END WHILE */

    /* USER CODE BEGIN 3 */
  }
  /* USER CODE END 3 */
}

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
/* USER CODE BEGIN Header_StartMainTask */
/**
  * @brief  Function implementing the mainTask thread.
  * @param  argument: Not used
  * @retval None
  */
/* USER CODE END Header_StartMainTask */
void StartMainTask(void *argument)
{
  /* init code for USB_DEVICE */
  MX_USB_DEVICE_Init();
  /* USER CODE BEGIN 5 */

  // CAuDri - If enabled, start recording traces used for debugging with Tracealyzer
  #ifdef DEBUG_USE_TRACE_RECORDER
    HAL_GPIO_WritePin(DEBUG_LED_BLUE_GPIO_Port, DEBUG_LED_BLUE_Pin, GPIO_PIN_SET);
    #ifdef DEBUG_WAIT_FOR_TRACEALYZER
      xTraceEnable(TRC_START_AWAIT_HOST);
    #else
      xTraceEnable(TRC_START_FROM_HOST);
    #endif
    // Initialize the logging interface with multiple trace channels
    extern void logger_trace_init();
    logger_trace_init();
    HAL_GPIO_WritePin(DEBUG_LED_BLUE_GPIO_Port, DEBUG_LED_BLUE_Pin, GPIO_PIN_RESET);
  #endif

  osDelay(10);

  // CAuDri - Initialize the thread-safe HAL wrapper
  if (!I2C_Init()) {
      LogError("Main: Failed to initialize thread-safe I2C wrapper");
  }
  if (!CAN_Init()) {
      LogError("Main: Failed to initialize thread-safe CAN wrapper");
  }

  osDelay(10);

  // CAuDri - Jump to our main entry point in main.cpp
  mainTask();

  /* Infinite loop */
  for(;;)
  {
    osDelay(1);
  }
  /* USER CODE END 5 */
}

/**
  * @brief  Period elapsed callback in non blocking mode
  * @note   This function is called  when TIM14 interrupt took place, inside
  * HAL_TIM_IRQHandler(). It makes a direct call to HAL_IncTick() to increment
  * a global variable "uwTick" used as application time base.
  * @param  htim : TIM handle
  * @retval None
  */
void HAL_TIM_PeriodElapsedCallback(TIM_HandleTypeDef *htim)
{
  if (htim->Instance == TIM14)
  {
    HAL_IncTick();
  }
}

/**
  * @brief  This function is executed in case of error occurrence.
  * @retval None
  */
void Error_Handler(void)
{
  /* USER CODE BEGIN Error_Handler_Debug */
  /* User can add his own implementation to report the HAL error return state */
  __disable_irq();
  while (1)
  {
  }
  /* USER CODE END Error_Handler_Debug */
}
#ifdef USE_FULL_ASSERT
/**
  * @brief  Reports the name of the source file and the source line number
  *         where the assert_param error has occurred.
  * @param  file: pointer to the source file name
  * @param  line: assert_param error line source number
  * @retval None
  */
void assert_failed(uint8_t *file, uint32_t line)
{
  /* USER CODE BEGIN 6 */
  /* User can add his own implementation to report the file name and line number,
     ex: printf("Wrong parameters value: file %s on line %d\r\n", file, line) */
  /* USER CODE END 6 */
}
#endif /* USE_FULL_ASSERT */

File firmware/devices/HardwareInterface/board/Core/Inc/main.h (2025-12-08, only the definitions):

#define I2C1_GPIO3_Pin GPIO_PIN_2
#define I2C1_GPIO3_GPIO_Port GPIOE
#define I2C1_GPIO3_EXTI_IRQn EXTI2_IRQn
#define I2C1_GPIO4_Pin GPIO_PIN_3
#define I2C1_GPIO4_GPIO_Port GPIOE
#define I2C1_GPIO5_Pin GPIO_PIN_4
#define I2C1_GPIO5_GPIO_Port GPIOE
#define I2C1_GPIO5_EXTI_IRQn EXTI4_IRQn
#define I2C1_GPIO6_Pin GPIO_PIN_5
#define I2C1_GPIO6_GPIO_Port GPIOE
#define I2C1_GPIO7_Pin GPIO_PIN_6
#define I2C1_GPIO7_GPIO_Port GPIOE
#define I2C1_GPIO7_EXTI_IRQn EXTI9_5_IRQn
#define I2C1_GPIO8_Pin GPIO_PIN_13
#define I2C1_GPIO8_GPIO_Port GPIOC
#define I2C2_GPIO1_Pin GPIO_PIN_5
#define I2C2_GPIO1_GPIO_Port GPIOF
#define I2C2_GPIO1_EXTI_IRQn EXTI9_5_IRQn
#define I2C2_GPIO2_Pin GPIO_PIN_6
#define I2C2_GPIO2_GPIO_Port GPIOF
#define I2C2_GPIO3_Pin GPIO_PIN_7
#define I2C2_GPIO3_GPIO_Port GPIOF
#define I2C2_GPIO3_EXTI_IRQn EXTI9_5_IRQn
#define I2C2_GPIO4_Pin GPIO_PIN_8
#define I2C2_GPIO4_GPIO_Port GPIOF
#define I2C2_GPIO5_Pin GPIO_PIN_9
#define I2C2_GPIO5_GPIO_Port GPIOF
#define I2C2_GPIO5_EXTI_IRQn EXTI9_5_IRQn
#define I2C2_GPIO6_Pin GPIO_PIN_0
#define I2C2_GPIO6_GPIO_Port GPIOC
#define I2C2_GPIO7_Pin GPIO_PIN_1
#define I2C2_GPIO7_GPIO_Port GPIOC
#define I2C2_GPIO7_EXTI_IRQn EXTI1_IRQn
#define I2C2_GPIO8_Pin GPIO_PIN_2
#define I2C2_GPIO8_GPIO_Port GPIOC
#define ANALOG_IN1_Pin GPIO_PIN_0
#define ANALOG_IN1_GPIO_Port GPIOA
#define ANALOG_IN2_Pin GPIO_PIN_1
#define ANALOG_IN2_GPIO_Port GPIOA
#define SERVO1_ADC_Pin GPIO_PIN_4
#define SERVO1_ADC_GPIO_Port GPIOA
#define SERVO2_ADC_Pin GPIO_PIN_5
#define SERVO2_ADC_GPIO_Port GPIOA
#define SERVO1_PWM_Pin GPIO_PIN_6
#define SERVO1_PWM_GPIO_Port GPIOA
#define SERVO2_PWM_Pin GPIO_PIN_7
#define SERVO2_PWM_GPIO_Port GPIOA
#define PWR_EXT_FAULT_Pin GPIO_PIN_11
#define PWR_EXT_FAULT_GPIO_Port GPIOF
#define PWR_EXT_FAULT_EXTI_IRQn EXTI15_10_IRQn
#define PWR_STATUS_Pin GPIO_PIN_12
#define PWR_STATUS_GPIO_Port GPIOF
#define PWR_STATUS_EXTI_IRQn EXTI15_10_IRQn
#define GPIO1_Pin GPIO_PIN_13
#define GPIO1_GPIO_Port GPIOF
#define GPIO1_EXTI_IRQn EXTI15_10_IRQn
#define GPIO2_Pin GPIO_PIN_14
#define GPIO2_GPIO_Port GPIOF
#define GPIO2_EXTI_IRQn EXTI15_10_IRQn
#define GPIO3_Pin GPIO_PIN_15
#define GPIO3_GPIO_Port GPIOF
#define GPIO3_EXTI_IRQn EXTI15_10_IRQn
#define SPI_IO1_Pin GPIO_PIN_10
#define SPI_IO1_GPIO_Port GPIOE
#define SPI_IO2_Pin GPIO_PIN_11
#define SPI_IO2_GPIO_Port GPIOE
#define PWR_EXT_ENABLE_Pin GPIO_PIN_12
#define PWR_EXT_ENABLE_GPIO_Port GPIOB
#define USB2_VBUS_Pin GPIO_PIN_13
#define USB2_VBUS_GPIO_Port GPIOB
#define USB2_D__Pin GPIO_PIN_14
#define USB2_D__GPIO_Port GPIOB
#define USB2_D_B15_Pin GPIO_PIN_15
#define USB2_D_B15_GPIO_Port GPIOB
#define TIM2_GPIO_Pin GPIO_PIN_10
#define TIM2_GPIO_GPIO_Port GPIOD
#define LED1_PWM_Pin GPIO_PIN_14
#define LED1_PWM_GPIO_Port GPIOD
#define LED2_PWM_Pin GPIO_PIN_15
#define LED2_PWM_GPIO_Port GPIOD
#define DEBUG_LED_BLUE_Pin GPIO_PIN_4
#define DEBUG_LED_BLUE_GPIO_Port GPIOG
#define DEBUG_LED_GREEN_Pin GPIO_PIN_5
#define DEBUG_LED_GREEN_GPIO_Port GPIOG
#define DEBUG_LED_RED_Pin GPIO_PIN_6
#define DEBUG_LED_RED_GPIO_Port GPIOG
#define TIM8_IO_Pin GPIO_PIN_8
#define TIM8_IO_GPIO_Port GPIOC
#define USER_BUTTON_Pin GPIO_PIN_8
#define USER_BUTTON_GPIO_Port GPIOA
#define USER_BUTTON_EXTI_IRQn EXTI9_5_IRQn
#define USB1_VBUS_Pin GPIO_PIN_9
#define USB1_VBUS_GPIO_Port GPIOA
#define USB1_D__Pin GPIO_PIN_11
#define USB1_D__GPIO_Port GPIOA
#define USB1_D_A12_Pin GPIO_PIN_12
#define USB1_D_A12_GPIO_Port GPIOA
#define SWD_SWDIO_Pin GPIO_PIN_13
#define SWD_SWDIO_GPIO_Port GPIOA
#define SWD_SWCLK_Pin GPIO_PIN_14
#define SWD_SWCLK_GPIO_Port GPIOA
#define UART3_GPIO_Pin GPIO_PIN_12
#define UART3_GPIO_GPIO_Port GPIOC
#define UART2_GPIO_Pin GPIO_PIN_3
#define UART2_GPIO_GPIO_Port GPIOD
#define UART2_GPIO_EXTI_IRQn EXTI3_IRQn
#define UART6_GPIO_Pin GPIO_PIN_10
#define UART6_GPIO_GPIO_Port GPIOG
#define UART6_GPIO_EXTI_IRQn EXTI15_10_IRQn
#define SWD_SWO_Pin GPIO_PIN_3
#define SWD_SWO_GPIO_Port GPIOB
#define I2C1_GPIO1_Pin GPIO_PIN_0
#define I2C1_GPIO1_GPIO_Port GPIOE
#define I2C1_GPIO1_EXTI_IRQn EXTI0_IRQn
#define I2C1_GPIO2_Pin GPIO_PIN_1
#define I2C1_GPIO2_GPIO_Port GPIOE

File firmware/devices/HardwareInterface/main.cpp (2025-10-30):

/**
 * @file main.cpp
 *
 * @brief CAuDri - Main entry point for the application code
 */

#include "main.h"

#include "config/config.h"
#include "logger.h"

#include <algorithm>

// CAuDri - This is necessary for OpenOCD to show the correct FreeRTOS task list
// TODO: Find a better place for this (must be linked into the final binary)
const volatile UBaseType_t uxTopUsedPriority = configMAX_PRIORITIES - 1;

extern "C" void mainTask();

RCReceiver rc_receiver;
VESC motor("VESC Driver");
Servo servo("Servo Front");

static bool rc_control_enabled = false;

// Callback for channel 5
void remoteSwitchCallback(uint16_t value) {
    if (value > 1500) {
        HAL_GPIO_WritePin(DEBUG_LED_RED_GPIO_Port, DEBUG_LED_RED_Pin, GPIO_PIN_RESET);
        HAL_GPIO_WritePin(DEBUG_LED_GREEN_GPIO_Port, DEBUG_LED_GREEN_Pin, GPIO_PIN_RESET);
        HAL_GPIO_WritePin(DEBUG_LED_BLUE_GPIO_Port, DEBUG_LED_BLUE_Pin, GPIO_PIN_SET);
        rc_control_enabled = false;
    } else if (value > 900) {
        HAL_GPIO_WritePin(DEBUG_LED_RED_GPIO_Port, DEBUG_LED_RED_Pin, GPIO_PIN_RESET);
        HAL_GPIO_WritePin(DEBUG_LED_GREEN_GPIO_Port, DEBUG_LED_GREEN_Pin, GPIO_PIN_SET);
        HAL_GPIO_WritePin(DEBUG_LED_BLUE_GPIO_Port, DEBUG_LED_BLUE_Pin, GPIO_PIN_RESET);
        rc_control_enabled = true;
    } else {
        HAL_GPIO_WritePin(DEBUG_LED_RED_GPIO_Port, DEBUG_LED_RED_Pin, GPIO_PIN_SET);
        HAL_GPIO_WritePin(DEBUG_LED_GREEN_GPIO_Port, DEBUG_LED_GREEN_Pin, GPIO_PIN_RESET);
        HAL_GPIO_WritePin(DEBUG_LED_BLUE_GPIO_Port, DEBUG_LED_BLUE_Pin, GPIO_PIN_RESET);
        motor.setRPM(0);
        rc_control_enabled = false;
    }
}

void motorChannelCallback(uint16_t value) {
    if (!rc_control_enabled) {
        // motor.setRPM(0);
        return;
    }

    LogInfo("Motor Channel Value: %d", value);

    if (value < 1050 && value > 950) {
        // Deadband around center
        motor.setRPM(0);
        return;
    }

    // Map RC channel value (200-1800) to RPM ~(-3000 to 3000)
    int32_t rpm = (static_cast<int32_t>(value) - 1000) * 3;

    // Clamp RPM to [-3000, 3000]
    if (rpm > 3000) {
        rpm = 3000;
    } else if (rpm < -3000) {
        rpm = -3000;
    }

    LogInfo("Motor RPM: %d, value: %d", rpm, value);
    motor.setRPM(rpm);
}

void steeringChannelCallback(uint16_t value) {
    if (!rc_control_enabled) {
        return;
    }

    // Map RC channel value (100-1900) to pulse width (1200-1800)
    uint32_t pulse_width = (static_cast<uint32_t>(value) - 100) * 600 / 1800 + 1200;
    LogInfo("Steering Pulse Width Command: %u", pulse_width);
    servo.setPulseWidth(pulse_width);
}


/**
 * @brief Main entry point called from the RTOS task in main.c
 */
void mainTask() {
    printf("Main Task: Starting up...\n");

    // Enable power for external components
    osDelay(100);
    HAL_GPIO_WritePin(PWR_EXT_ENABLE_GPIO_Port, PWR_EXT_ENABLE_Pin, GPIO_PIN_SET);
    osDelay(100);

    rc_receiver.init(rc_config);

    motor.init(vesc_config);
    motor.start();

    servo.init(servo_config, servo_calibration);

    rc_receiver.registerChannelCallback(6, RCReceiver::ChannelCallback::from<&remoteSwitchCallback>(), true);
    rc_receiver.registerChannelCallback(1, RCReceiver::ChannelCallback::from<&motorChannelCallback>(), true);
    rc_receiver.registerChannelCallback(3, RCReceiver::ChannelCallback::from<&steeringChannelCallback>(), true);
    rc_receiver.start();

    for (;;) {
        osDelay(2000);
        // static uint16_t angle = 0;
        // angle += 10;
        // if (angle > 180) {
        //     angle = 0;
        // }
        // servo.setAngle(static_cast<float>(angle));

        // CAN_TxHeaderTypeDef tx_header{};
        // uint8_t tx_data[8] = {0x11, 0x22, 0x33, 0x44, 0x55, 0x66, 0x77, 0x88};
        // uint32_t tx_mailbox;
        // tx_header.StdId = 0x123;
        // tx_header.ExtId = 0x123456;
        // tx_header.IDE = CAN_ID_EXT;
        // tx_header.RTR = CAN_RTR_DATA;
        // tx_header.DLC = 8;
        // HAL_CAN_AddTxMessage(&hcan1, &tx_header, tx_data, &tx_mailbox);

        // HAL_GPIO_TogglePin(DEBUG_LED_BLUE_GPIO_Port, DEBUG_LED_BLUE_Pin);

        // auto can_state = HAL_CAN_GetState(&hcan1);
        // switch (can_state) {
        //     case HAL_CAN_STATE_RESET:
        //         LogInfo("CAN1 State: RESET");
        //         break;
        //     case HAL_CAN_STATE_READY:
        //         LogInfo("CAN1 State: READY");
        //         break;
        //     case HAL_CAN_STATE_LISTENING:
        //         LogInfo("CAN1 State: LISTENING");
        //         break;
        //     case HAL_CAN_STATE_SLEEP_PENDING:
        //         LogInfo("CAN1 State: SLEEP_PENDING");
        //         break;
        //     case HAL_CAN_STATE_SLEEP_ACTIVE:
        //         LogInfo("CAN1 State: SLEEP_ACTIVE");
        //         break;
        //     case HAL_CAN_STATE_ERROR:
        //         LogInfo("CAN1 State: ERROR");
        //         break;
        //     default:
        //         LogInfo("CAN1 State: UNKNOWN, state value: %d", static_cast<int>(can_state));
        //         break;
        // }

        // auto can_error = HAL_CAN_GetError(&hcan1);
        // LogInfo("CAN1 Error Code: 0x%08lX", can_error);

        // CAN_RxHeaderTypeDef rx_header;
        // uint8_t rx_data[8];
        // if (HAL_CAN_GetRxFifoFillLevel(&hcan1, CAN_RX_FIFO0) > 0) {
        //     auto rx_message = HAL_CAN_GetRxMessage(&hcan1, CAN_RX_FIFO0, &rx_header, rx_data);
        //     if (rx_message == HAL_OK) {
        //         LogInfo("CAN1 RX Message Pending: ID=0x%08lX, DLC=%u", rx_header.ExtId, rx_header.DLC);
        //     } else {
        //         LogInfo("CAN1 RX Message Pending: None");
        //     }
        // }

        // bool tx0_pending = HAL_CAN_IsTxMessagePending(&hcan1, CAN_TX_MAILBOX0 );
        // bool tx1_pending = HAL_CAN_IsTxMessagePending(&hcan1, CAN_TX_MAILBOX1 );
        // bool tx2_pending = HAL_CAN_IsTxMessagePending(&hcan1, CAN_TX_MAILBOX2 );
        // LogInfo("CAN1 TX Message Pending on Mailboxes: 0=%s, 1=%s, 2=%s",
        //         tx0_pending ? "YES" : "NO",
        //         tx1_pending ? "YES" : "NO",
        //         tx2_pending ? "YES" : "NO");

        // motor.setRPM(1000);

        // crsf::ChannelData channels;
        // if (rc_receiver.getChannelData(channels)) {
        //     LogInfo("%u %u %u %u", channels[0], channels[1], channels[2], channels[3]);
        //     LogInfo("%u %u %u %u", channels[4], channels[5], channels[6], channels[7]);
        //     LogInfo("%u %u %u %u", channels[8], channels[9], channels[10], channels[11]);
        //     LogInfo("%u %u %u %u", channels[12], channels[13], channels[14], channels[15]);

        // } else {
        //     LogWarning("Failed to get channel data");
        // }
        // LogInfo("Main task running...");
    }
}

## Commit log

2025-06-16 add initial PCB files
    [LARS_Analog.kicad_sch, LARS_Bus.kicad_sch, LARS_IO_Protection.kicad_sch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]
2025-06-16 move PCB design files to KiCad folder
    [LARS_Analog.kicad_sch, LARS_Bus.kicad_sch, LARS_IO_Protection.kicad_sch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]
2025-06-17 update to KiCad 9.0
    [LARS_Analog.kicad_sch, LARS_Bus.kicad_sch, LARS_IO_Protection.kicad_sch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]
2025-06-19 add symbol and footprint libraries
2025-06-20 Initial Repo Setup
    [LARS_Analog.kicad_sch, LARS_Bus.kicad_sch, LARS_IO_Protection.kicad_sch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]
2025-06-20 Revert "Merge branch 'main_tmp' into 'main'"
    This reverts merge request !1
    [LARS_Analog.kicad_sch, LARS_Bus.kicad_sch, LARS_IO_Protection.kicad_sch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]
2025-06-20 reannotate schematic
    [LARS_Bus.kicad_sch, LARS_IO_Protection.kicad_sch, LARS_IO_interfaces.kicad_sch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]
2025-06-20 add differential pairs and power traces
    [hardware_interface.kicad_pcb]
2025-06-22 add final traces
    [LARS_Analog.kicad_sch, LARS_IO_Protection.kicad_sch, LARS_IO_interfaces.kicad_sch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]
2025-06-23 update PCB layout
2025-06-27 finish PCB routing
    [LARS_Bus.kicad_sch, LARS_LEDs.kicad_sch, LARS_Microcontroller.kicad_sch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]
2025-06-27 change default KiCad schematic font
    [LARS_Analog.kicad_sch, LARS_Bus.kicad_sch, LARS_IO_Protection.kicad_sch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]
2025-06-27 update text layout and fix remaining DRC errors
    [LARS_Analog.kicad_sch, LARS_Bus.kicad_sch, LARS_IO_Protection.kicad_sch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]
2025-06-27 add manufacturing files for JLCPCB
    [bom.csv, designators.csv, positions.csv]
2025-06-27 add schematic and rendered board images
2025-08-12 add ESD protection and update footprints
    [LARS_Analog.kicad_sch, LARS_Bus.kicad_sch, LARS_IO_Protection.kicad_sch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]
2025-08-12 update JLCPCB manufacturing files
    [bom.csv, designators.csv, positions.csv]
2025-10-02 add udev rules for serial device access
2025-10-02 move CMakeLists.txt to top level device directory and add .hex and .bin conversion
2025-10-02 add udev rule for the STM32 DFU bootloader
2025-10-02 update OpenOCD config to use a CMSIS-DAP device by default
2025-10-02 add trace recorder library and CMakeLists.txt
2025-10-02 add trace recorder init and jump to main application entry
2025-10-02 add thread-safe logging interface
2025-10-02 enable EXTI interrupts in CubeMX and change USB device descriptor
2025-10-02 enable UART callback registering
2025-10-02 enable global UART interrupts
2025-10-02 fully integrate Tracelyzer trace recorder library
2025-10-02 enable printf float formatting and set C99 standard
2025-10-02 add common driver interface
2025-10-02 add initial CRSF/Remote Control driver
2025-10-28 add thread-safe I2C wrapper
2025-10-28 add thread-safe CAN bus wrapper and RX dispatcher
2025-10-29 enable CAN interrupts in CubeMX
2025-10-30 add init for thread safe HAL extensions
2025-10-30 add initial servo driver implementation
2025-10-30 add initial VESC driver implementation
2025-10-30 update main.cpp with exmaple driver test
2025-11-15 lower log verbosity for the thread-safe CAN interface
2025-11-15 add connection state handling to driver interface
2025-11-27 PCB: update resistor values and embed font
    [LARS_Analog.kicad_sch, LARS_Bus.kicad_sch, LARS_IO_Protection.kicad_sch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]
2025-11-27 PCB: fix silkscreen pinout for servo and CAN connectors
    [hardware_interface.kicad_pcb]
2025-11-29 PCB: change revision and dates
    [hardware_interface.kicad_pcb, hardware_interface.kicad_sch]
2025-11-30 PCB: update drawing sheet
    [LARS_Analog.kicad_sch, LARS_Bus.kicad_sch, LARS_IO_Protection.kicad_sch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]
2025-11-30 PCB: add manufacturing files for v1.1
    [hardware_interface_bom.csv, hardware_interface_designators.csv, hardware_interface_positions.csv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]
2025-11-30 PCB: update exported files
    [hardware_interface.kicad_pcb]
2025-11-30 PCB: fix manufacturing files for v1.1
    [hardware_interface_bom.csv]
2025-11-30 add simple state handling and safety to VESC driver
2025-11-30 fix trace recorder init for globally declared driver instances
2025-12-04 update CubeMX and HAL version and link DMA stream for WS2812
2025-12-06 add DriveController for mode switch and motor control
2025-12-06 add driver for WS2812
2025-12-06 add WS2812 Light implementation for subsets of a LED string
2025-12-07 fix VESC callback registering and add remaining status handlers
2025-12-07 add proper connection state handling to VESC driver
2025-12-08 add Light interface implementation for single GPIO controlled LEDs
2025-12-08 add verbose log to servo driver
2025-12-08 add missing DMA stream declaration to main.h
    [main.h]
2025-12-12 enable TIM5 for ADC sampling
2025-12-13 enable DMA streams for ADC peripherals
2026-02-03 PCB: move LED2 to timer peripheral 1 and update pinout
    [hardware_interface.kicad_sch]
2026-02-27 PCB: add XOR gate for RC Receiver
    [LARS_Bus.kicad_sch, LARS_IO_Protection.kicad_sch, LARS_IO_interfaces.kicad_sch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]
2026-02-27 update .ioc with new pin layout
2026-03-08 PCB: update manufacturing files
    [LARS_IO_Protection.kicad_sch, hardware_interface.kicad_pcb, hardware_interface.kicad_sch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]

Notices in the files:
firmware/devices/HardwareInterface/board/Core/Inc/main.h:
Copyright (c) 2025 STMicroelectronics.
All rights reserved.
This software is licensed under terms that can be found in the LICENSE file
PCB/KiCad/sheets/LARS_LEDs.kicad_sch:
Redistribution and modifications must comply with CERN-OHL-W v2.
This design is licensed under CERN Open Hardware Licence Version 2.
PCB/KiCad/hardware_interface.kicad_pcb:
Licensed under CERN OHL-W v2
